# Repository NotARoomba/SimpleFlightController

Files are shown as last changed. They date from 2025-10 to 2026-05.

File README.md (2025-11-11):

<h1 align="center">
  <br>
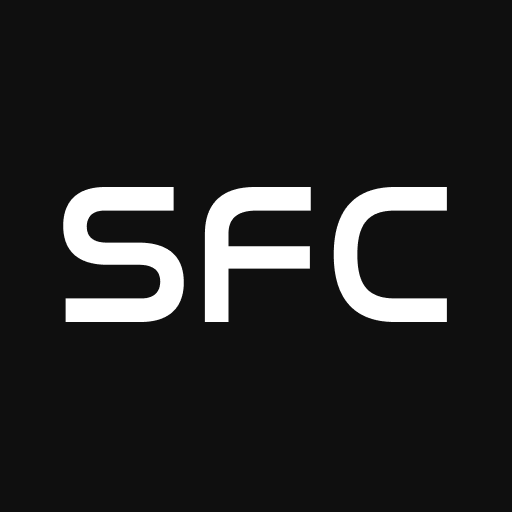
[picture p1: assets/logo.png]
SFC
  
  <br>
  Simple Flight Controller
  <br>
</h1>

<h4 align="center">
A comprehensive guide on building a flight controller from scratch for rockets!
</h4>

<div align="center">




</div>

<p align="center">
  <a href="#key-features">Key Features</a> •
  <a href="#guide">Guide</a> •
  <a href="#pcb">PCB</a> •
  <a href="#credits">Credits</a> •
  <a href="#license">License</a>
</p>

Flight Controller PCB

## Key Features

- **STM32F722RET6 microcontroller** for high-performance control
- **ICM-45686 IMU** for precise motion tracking
- **BMP580 barometer** for altitude sensing
- **MicroSD card storage** for flight data logging
- **Dual servo outputs** for TVC or fin control
- **2-cell LiPo support** with integrated BQ25883 charger
- **USB-C connectivity** for programming and data transfer
- **Compact design** optimized for rocket applications

## Guide

Check out the comprehensive [GUIDE.md](GUIDE.md) that walks you through:

- Component selection and requirements
- Schematic design with detailed explanations
- Communication protocols (I2C, SPI, UART, USB)
- PCB layout and routing best practices
- Power management circuitry
- Manufacturing with JLCPCB

## PCB

Designed in KiCad with careful attention to signal integrity, power distribution, and compact layout suitable for rocket applications.

### Schematic

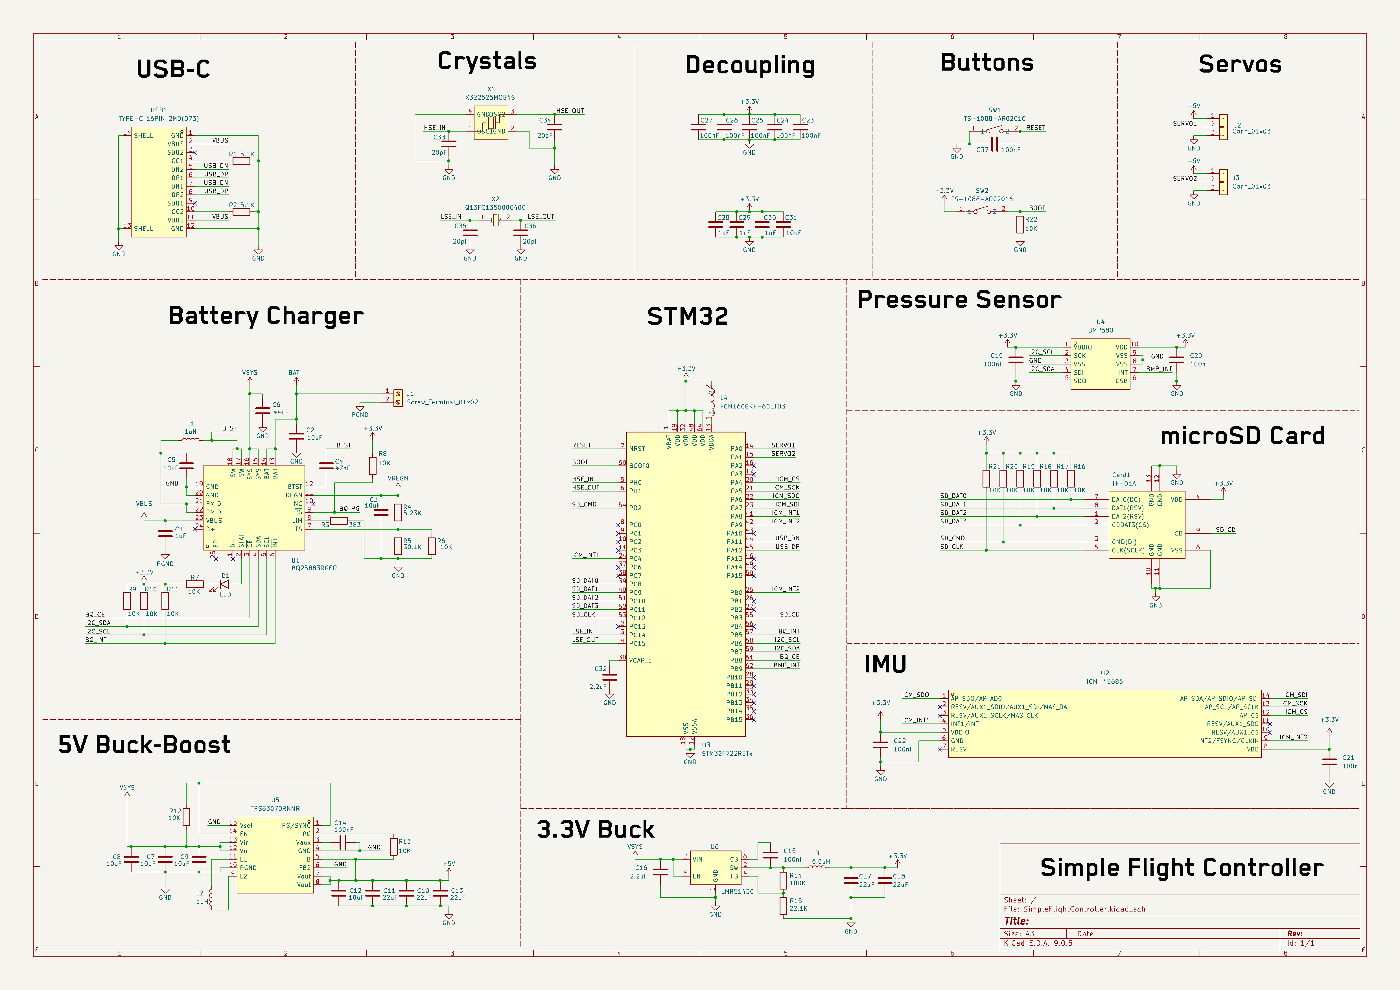
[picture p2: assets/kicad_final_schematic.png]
Schematic


### PCB Layout

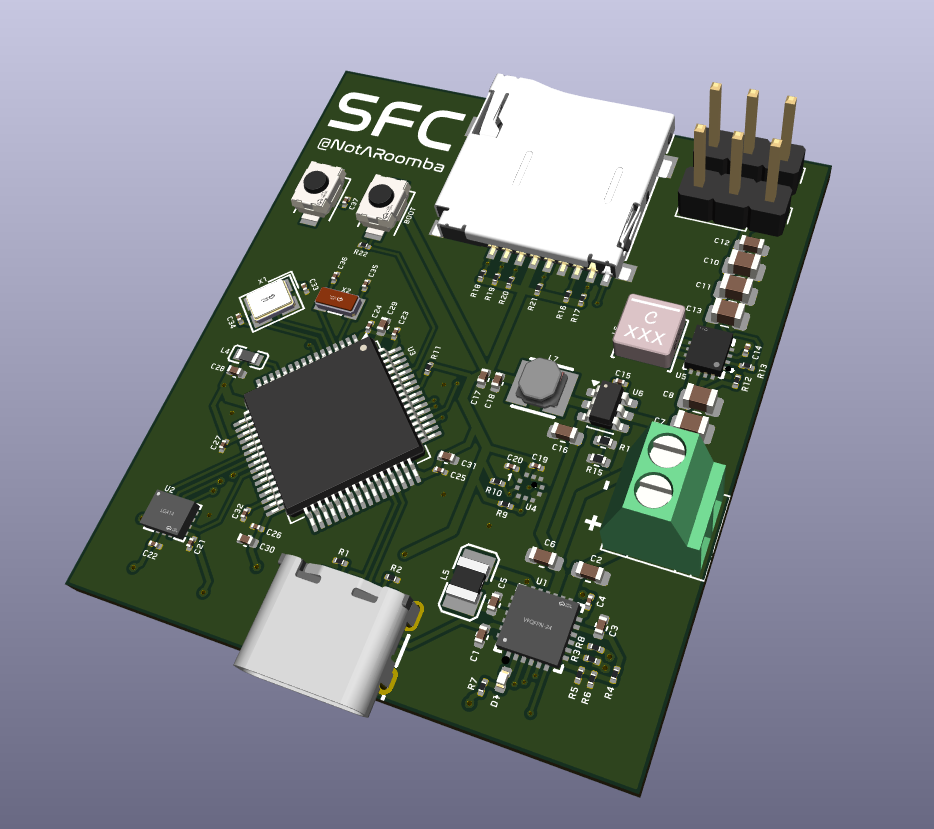
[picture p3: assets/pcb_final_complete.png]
PCB Layout


## Credits

This project uses:

- [KiCad](https://www.kicad.org/)
- [STM32CubeMX](https://www.st.com/en/development-tools/stm32cubemx.html)
- [easyeda2kicad.py](https://github.com/uPesy/easyeda2kicad.py)
- [Hack Club Blueprint](https://blueprint.hackclub.com/)

## You may also like...

- [Trace](https://github.com/NotARoomba/Trace) – A comprehensive PCB ruler with reference footprints
- [Cyberboard](https://github.com/NotARoomba/Cyberboard) – A Raspberry Pi Pico-sized STM32 development board with Bluetooth
- [CyberCard](https://github.com/NotARoomba/CyberCard) – A Cyberpunk themed NFC hacker card
- [Niveles De Niveles](https://github.com/NotARoomba/NivelesDeNiveles) – Real-time flood alert app
- [Linea](https://github.com/NotARoomba/Linea) – An EMR tablet
- [Tamaki](https://github.com/NotARoomba/Tamaki) – A cute HackPad

## License

MIT

---

> [notaroomba.dev](https://notaroomba.dev) &nbsp;&middot;&nbsp;
> GitHub [@NotARoomba](https://github.com/NotARoomba) &nbsp;&middot;&nbsp;

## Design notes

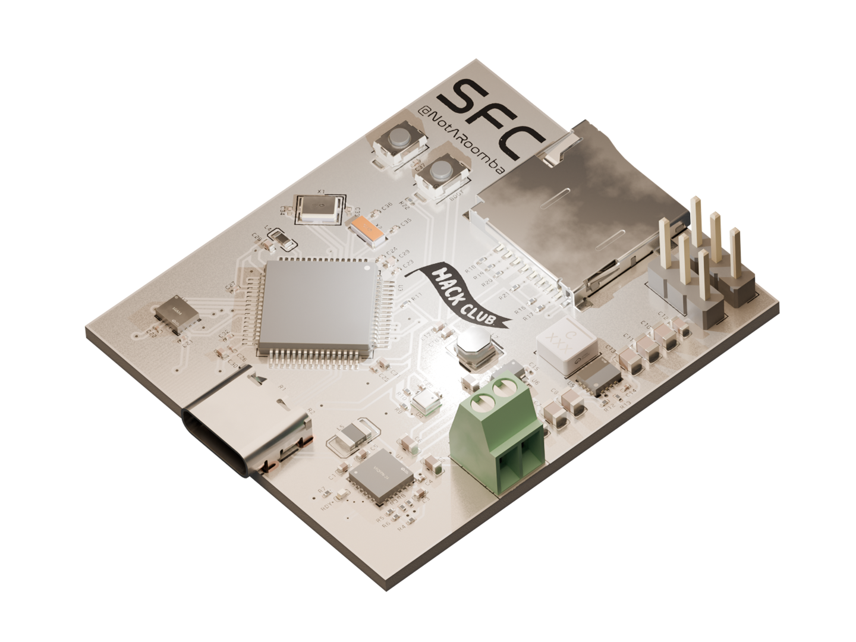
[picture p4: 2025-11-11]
blender/render_cropped.png

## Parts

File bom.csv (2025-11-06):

Item | Price | Source
PCB | 165.50 | JLCPCB

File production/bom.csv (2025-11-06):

Designator | Footprint | Quantity | Value | LCSC Part #
BOOT, RESET | SW-SMD_L3.9-W3.0-P4.45 | 2 | TS-1088-AR02016 | C720477
C1, C28, C29, C30 | 0402 | 4 | 1uF
C10, C11, C13 | 0805 | 3 | 22uF
C12, C2, C9 | 0603 | 3 | 10uF
C14, C15, C19, C20, C21, C22, C23, C24, C25, C26, C27, C37 | 0201 | 12 | 100nF
C16 | 0603 | 1 | 2.2uF
C17, C18 | 0402 | 2 | 22uF
C3, C31, C5 | 0402 | 3 | 10uF
C32 | 0201 | 1 | 2.2uF
C33, C34, C35, C36 | 0201 | 4 | 20pF
C4 | 0201 | 1 | 47nF
C6 | 0603 | 1 | 44uF
C7, C8 | 0805 | 2 | 10uF
CARD1 | TF-SMD_TF-01A | 1 | TF-01A | C91145
D1 | 0402 | 1 | LED
J1 | TerminalBlock_Xinya_XY308-2.54-2P_1x02_P2.54mm_Horizontal | 1 | Screw_Terminal_01x02
J2, J3 | PinHeader_1x03_P2.54mm_Vertical | 2 | Conn_01x03
L4 | L0603 | 1 | FCM1608KF-601T03 | C141723
L5 | L2520 | 1 | DFE252012F-1R0M=P2 | C435392
L6 | IND-SMD_L4.0-W4.0-A | 1 | XFL4020-152MEC | C3033018
L7 | IND-SMD_L3.0-W3.0 | 1 | YHNR3015-5R6M | C18236327
R1, R2 | 0201 | 2 | 5.1K
R10, R11, R12, R13, R16, R17, R18, R19, R20, R21, R22, R6, R7, R8, R9 | 0201 | 15 | 10K
R14 | 0402 | 1 | 100K
R15 | 0402 | 1 | 22.1K
R3 | 0201 | 1 | 383
R4 | 0201 | 1 | 5.23K
R5 | 0201 | 1 | 30.1K
U1 | VFQFPN-24_L4.0-W4.0-P0.50-BL-EP2.8 | 1 | BQ25883RGER | C544362
U2 | LGA-14_L3.0-W2.5-P0.50-TL | 1 | ICM-45686 | C22459454
U3 | LQFP-64_10x10mm_P0.5mm | 1 | STM32F722RETx
U4 | LGA-10_L2.0-W2.0-P0.50-TL_BMP580 | 1 | BMP580 | C22391138
U5 | VQFN-HR-15_L3.0-W2.5-P0.50-BL_TPS63070RNMR | 1 | TPS63070RNMR | C109322
U6 | SOT-23-6 | 1 | LMR51430
USB1 | USB-C-SMD_TYPE-C-6PIN-2MD-073 | 1 | TYPE-C 16PIN 2MD(073) | C2765186
X1 | CRYSTAL-SMD_4P-L3.2-W2.5-BL | 1 | X322525MOB4SI | C9006
X2 | FC-135R_L3.2-W1.5 | 1 | Q13FC1350000400 | C32346

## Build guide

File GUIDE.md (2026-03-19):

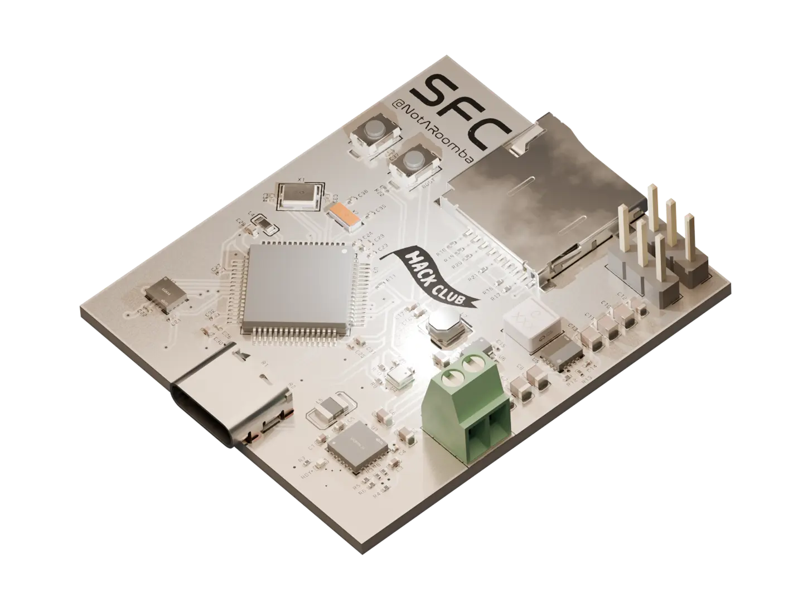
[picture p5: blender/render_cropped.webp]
Flight Controller Render


# How to make a flight controller (from scratch)

Made by @NotARoomba

This is an advanced project. I recommend learning the basics of KiCad by making a small dev board or breadboard first. That said, anyone can follow along, as I'll go **_in-depth_** on how to build a flight controller.

I'm [@NotARoomba](https://github.com/notaroomba) and I have a (sort of) obsession with making flight controllers so heres a guide so that you too have the knowledge of making something [cool](https://github.com/notaroomba/athena). The files for this guide can be found [here](https://github.com/notaroomba/simpleflightcontroller)

First, define what type of flight controller you want: for a rocket or a drone? Keep that in mind when starting your own design. In this guide, we'll build a flight controller specifically for rockets.

To start, create a new repository on GitHub and add two folders: `hardware` and `software`. These folders will hold most of the project files. Then, create a new KiCad project inside the `hardware` folder.

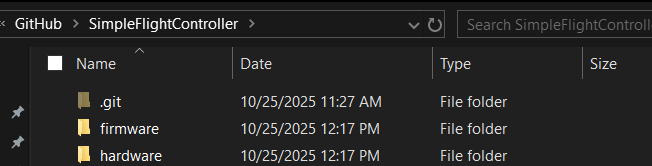
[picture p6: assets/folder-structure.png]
Folder Structure

(Folder structure)

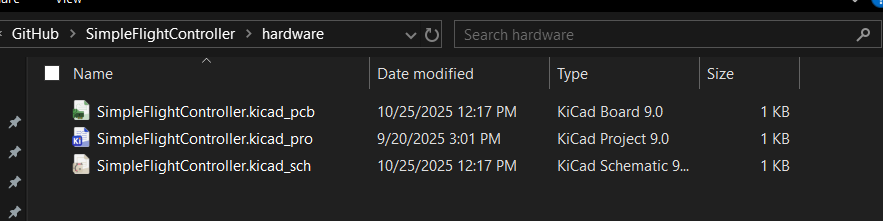
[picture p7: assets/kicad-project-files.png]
KiCad Project Files

(KiCad project files)

## Feature Definition

Before starting any engineering project, define the problem you're solving and the constraints you have. Imagine you want to build a rocket. All flight controllers include a `microcontroller`, which is a small computer that can be programmed to do various tasks. To control the rocket's flight, you'll use servos to move fins or a TVC system (`Thrust Vector Control`- tilting the engine nozzle to steer the rocket).

If you only build a board to drive servos, the rocket won't know which way it's pointing or how to correct its trajectory. You also need position and motion data (rotation and acceleration), plus altitude data. Finally, you'll want to store data persistently (even when powered off) for debugging and post-flight analysis.

Now that we have the rocket's functionality defined, we also need a way to power it. We can use a battery that can power both the rocket's computer and its servos.

Putting this together, we want these features in our rocket's flight controller:

- Can control servos for fins or TVC
- Can obtain position and altitude data
- Can store data even when powered off
- Can be powered by a battery

## Next steps

Now that we have our requirements, let's see how to meet them. Some requirements depend on others. For example, we want battery power - but how large should the battery be? That depends on the voltages and current the servos and microcontroller need, so let's define those first.

Depending on the size of your rocket, current needs will vary because larger servos draw more current. Most hobby servos run on 5–6V and draw ~1A. A 2-cell LiPo (Lithium Polymer) battery (7.4V nominal) is common in RC applications (each cell is ~3.7V) and can be regulated down to 5V for servos.

Most microcontrollers and sensors run on 3.3V, so with a 2-cell (7.4V) LiPo we have more than enough input voltage—as long as we regulate it down to a clean 3.3V line.

Now, after checking off one of the features, we need to tackle the three others.

- Can control servos for fins or TVC
- Can obtain position/altitude data
- Can store data even when powered off
- ~~Can be powered by a battery~~

After choosing servos, we need to know how to control them. Most hobby servos use `PWM (Pulse Width Modulation)`—a method of control where the microcontroller sends rapid on/off pulses, and the pulse width (duration) determines the servo's position.

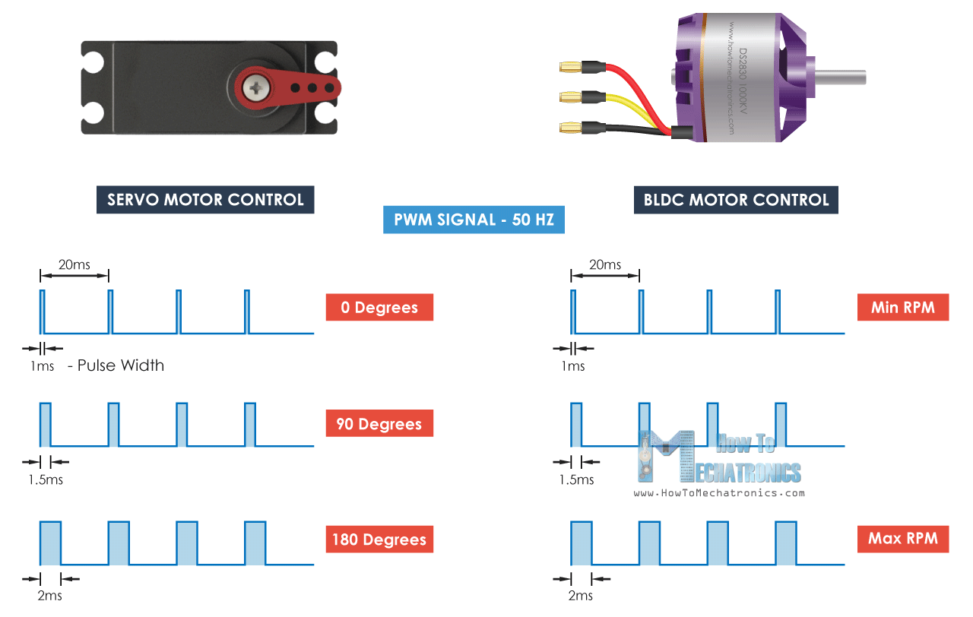
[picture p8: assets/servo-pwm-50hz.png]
Servo PWM Signal


The `duty cycle` is the percentage of the period that the signal is high (on).

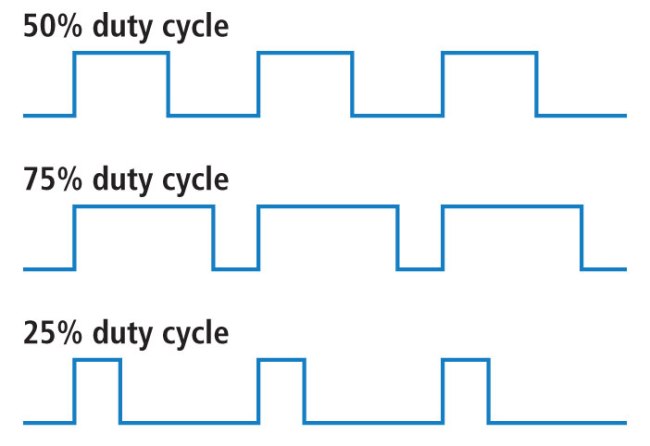
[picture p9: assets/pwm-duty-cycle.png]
PWM Duty Cycle


## What about the sensors and microcontroller?

- ~~Needs to be able to control servos for fins or TVC~~
- Needs a way to get position/altitude data
- Needs to store data even when the rocket is off
- ~~Needs to be able to be powered by a battery~~

For position and motion data, we use an `IMU`—an Inertial Measurement Unit. The IMU measures acceleration and rotation (and some devices also estimate altitude). We'll use the `ICM-45686`. While there are many IMUs with different features, this one is robust and well-supported.

For altitude, we'll use a dedicated sensor called a barometer. It measures air pressure and uses that to estimate altitude. We'll use the `BMP580`—a versatile and common choice for flight controllers.

Finally, to store data, we'll use a microSD card. While you can use onboard flash, microSD is more versatile when you want to access flight logs directly from a computer.

Now that we've defined the sensors and peripherals, we need to select a microcontroller. In this tutorial, we'll use an STM32, but you can adapt it to another MCU like the ESP32 if you want Bluetooth/Wi-Fi support. I prefer STM32 because it's relatively easy to program and widely used in flight controllers. After reviewing STM32 options, we'll use the STM32F722RET6 for its high clock speed and lots of peripherals. Feel free to choose another package or part for larger designs.

- ~~Needs to be able to control servos for fins or TVC~~
- ~~Needs a way to get position/altitude data~~
- ~~Needs to store data even when the rocket is off~~
- ~~Needs to be able to be powered by a battery~~

## Power Management

We have two power sources: USB-C from your computer (5V) and a battery (about 7–8.4V for a 2-cell LiPo). You cannot just wire them together. They need circuitry to choose which one feeds the board and to set the right voltages. The microcontroller typically runs at 3.3V, so we must lower the voltage (from the battery or USB-C) before it reaches the MCU.

To change the voltages, we need to use a regulator. There are two common kinds of regulators you'll hear about:

- `LDO`—Low Dropout regulator. It only turns higher voltage into a slightly lower one. Easy and quiet, but it wastes the excess as heat.
- `Switching regulator`—A more efficient regulator. It can:
  - `buck` (turn higher voltage down),
  - `boost` (push lower voltage up), or
  - `buck-boost` (keep the output steady even if the input goes above or below it).

What we'll do on this board:

- Make a 3.3V line (for the MCU and sensors) using a buck regulator.
- Make a 5V line (for servos or accessories) using a buck-boost regulator so it stays at 5V even as the battery voltage fluctuates.
- Get a battery charging IC (Integrated Circuit—a chip) that can charge a 2-cell battery from 5V.

Now that we've specified what functionality we need, we need to select the chips that provide it. I personally love to use ICs from Texas Instruments as they have good documentation and a huge selection of power management chips for everything related to USB.

Go to their website (https://www.ti.com/), select "Products", then "Battery Management ICs", and finally "Battery Charging ICs". Here you can find all sorts of battery charging chips to fit your requirements for future projects.

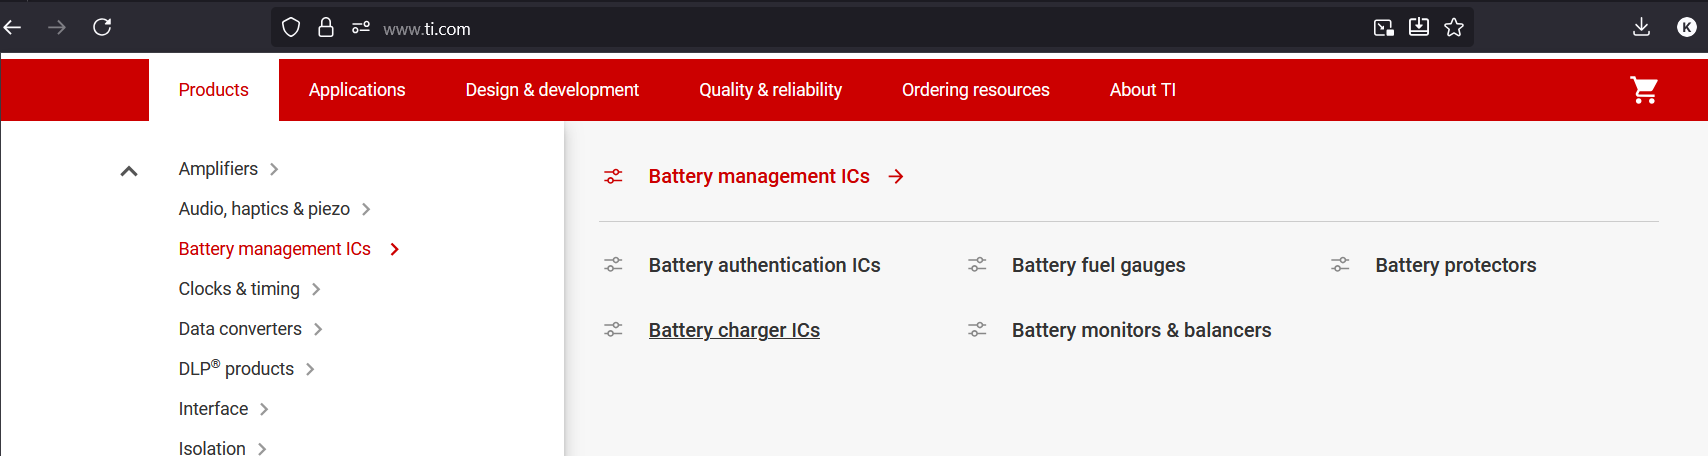
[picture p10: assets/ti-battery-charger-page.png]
TI Battery Charger Page


After looking around a bit, I found the `BQ25883`. It's a 2-cell Li-Ion/LiPo charger (which meets our requirement). You could add a more complicated battery charger if you want more cells/power, but they take up more space and are more complex to route.

For the regulators, go back to the TI main page, then navigate to "Power Management," then "DC/DC Power Modules." Here you can find all the regulators you would ever need, complete with excellent datasheets.

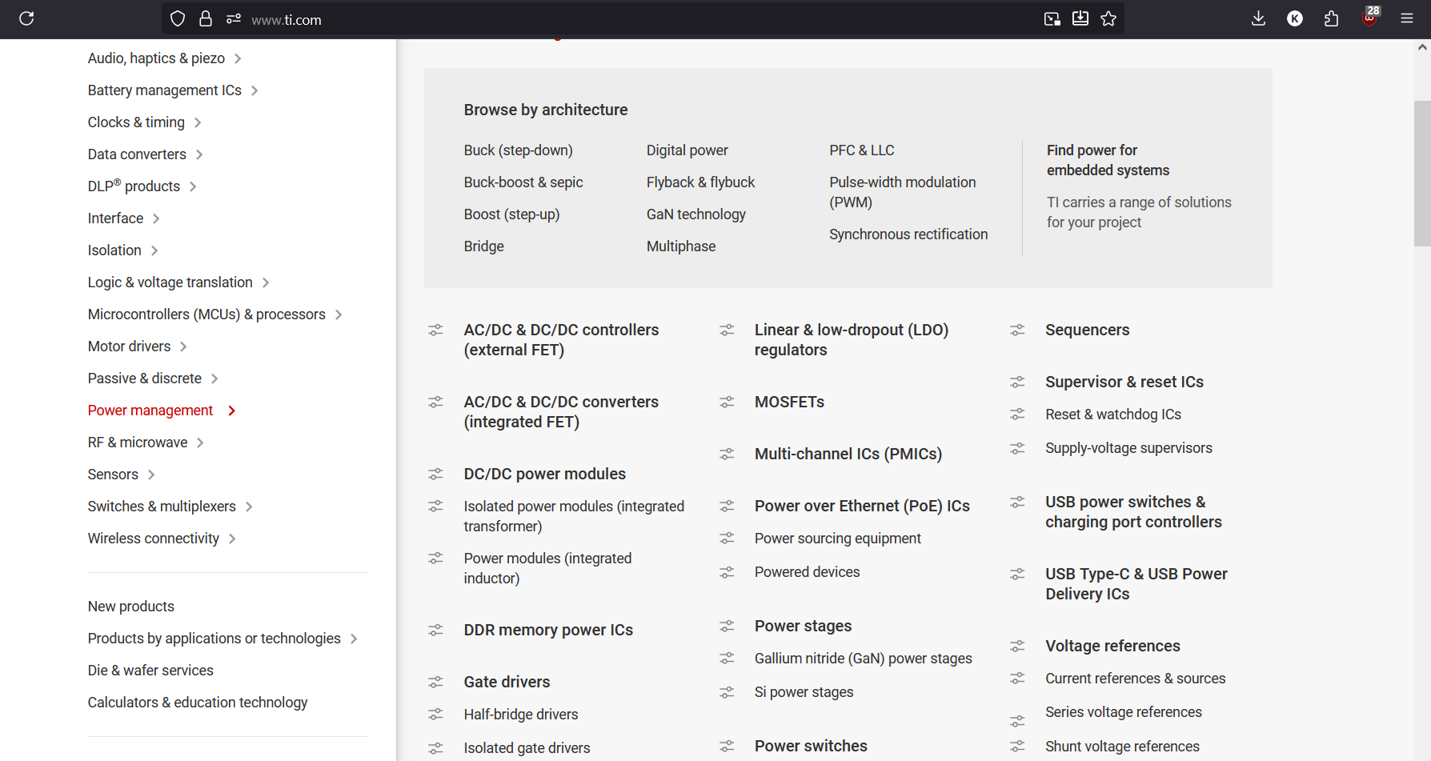
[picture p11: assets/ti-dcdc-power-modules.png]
TI DC/DC Power Modules


Here is where we can choose the right regulators for our needs. For this tutorial, we are going to use the `TPS63070`, which supports 2–16V input and can output a steady 5V with high current for the servos.

Now all that's missing is to find another regulator for 3.3V. For this, we are going to use the `LMR51430` as it supplies a lot of amperage for the various sensors that we will be using.

Now that we have the chips that we are going to use, we also need to verify that they are available on some platform like [LCSC](https://lcsc.com) or wherever else you are going to manufacture your PCB. We also might have to import certain components from LCSC into KiCad.

## Final component list

- USB-C
- MicroSD
- TPS63070
- LMR51430
- BQ25883
- STM32F722RETx
- ICM-45686
- BMP580
- Optional LED

# Starting the Schematic

Now that we have the components that we are going to use, let's start importing them into our project.

Although KiCad has a large selection of components, it is still a bit outdated and there are tons of chips that we would have to import in order to use them. Thankfully, there is a library called [`easyeda2kicad.py`](https://github.com/uPesy/easyeda2kicad.py) that can import these components from LCSC for us.

I have made a simple helper script to import all of the LCSC IDs from a text file, so all you have to do is append the part numbers and run the script again.

## Adding Custom Parts

Start by creating a folder called `lib` in the `/hardware` directory.

Then in the `/hardware` directory, create a new file called `lcsc.txt` and leave it empty for now.

Then create a file called `lcsc.py` (or whatever name you want) and paste this code in there:

```import argparse
import os
import shutil
import subprocess
import sys

def run_easyeda2kicad_from_file(input_file, output_dir="./lib/lcsc", python_exec="python"):
    input_file = os.path.expanduser(input_file)
    output_dir = os.path.expanduser(output_dir)
    python_exec = python_exec or "python"

    if not os.path.isfile(input_file):
        print(f"Error: File not found: {input_file}")
        return 2

    # If a simple name was provided, check PATH; if an absolute path, check that file exists.
    found = shutil.which(python_exec) if os.path.basename(python_exec) == python_exec else os.path.exists(python_exec)
    if not found:
        print(f"Warning: Python executable '{python_exec}' not found in PATH or as given path. Trying anyway.")

    os.makedirs(output_dir, exist_ok=True)

    with open(input_file, "r", encoding="utf-8") as f:
        # ignore blank lines and comments
        lines = [line.strip() for line in f if line.strip() and not line.lstrip().startswith("#")]

    if not lines:
        print("No LCSC IDs found in input file.")
        return 0

    for idx, lcsc_id in enumerate(lines, start=1):
        cmd = [
            python_exec,
            "-m", "easyeda2kicad",
            "--full",
            f"--lcsc_id={lcsc_id}",
            f"--output={output_dir}",
        ]
        print(f"[{idx}/{len(lines)}] Running: {' '.join(cmd)}")
        try:
            subprocess.run(cmd, check=True)
        except subprocess.CalledProcessError as e:
            print(f"❌ Error processing {lcsc_id}: {e}")
        except FileNotFoundError as e:
            print(f"❌ Executable not found: {e}")
            return 3

    print("✅ All commands completed.")
    return 0

def main(argv=None):
    parser = argparse.ArgumentParser(description="Run easyeda2kicad for a list of LCSC IDs.")
    parser.add_argument("input_file", nargs="?", default="./hardware/lcsc.txt", help="Path to file with one LCSC ID per line")
    parser.add_argument("output_dir", nargs="?", default="./lib/lcsc", help="Output directory")
    parser.add_argument("--python", dest="python_exec", default="python",
                        help="Python executable to use (default: 'python')")
    args = parser.parse_args(argv)

    return_code = run_easyeda2kicad_from_file(args.input_file, args.output_dir, args.python_exec)
    sys.exit(return_code if isinstance(return_code, int) else 0)

if __name__ == "__main__":
    main()
```

---

This code basically calls the `easyeda2kicad.py` library for every line that is present in `lcsc.txt` and adds it to a KiCad library in `/hardware/lib/lcsc`. (Make sure to install it first using `pip install easyeda2kicad.py`)

Now after creating both of those files, in your favorite IDE, edit `lcsc.txt` with the part numbers of the chips that you are going to use.

For example, let's say I want to add a USB-C port from LCSC. Go to [`www.lcsc.com`](www.lcsc.com) and search for USB-C.

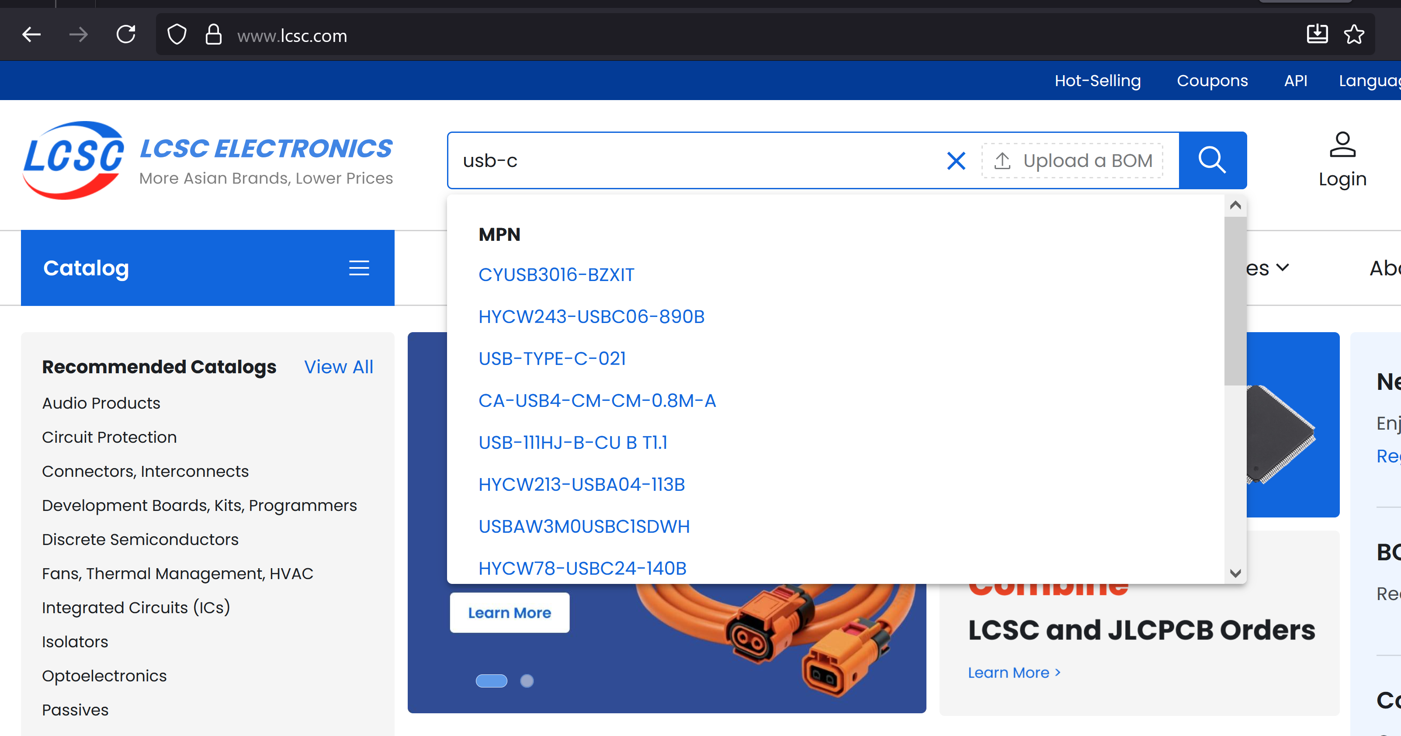
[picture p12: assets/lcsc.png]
LCSC Search


After searching, I found a good part with large stock (important!), so I then copy the part number (always starts with C followed by numbers, and it's under the name) into `lcsc.txt`.

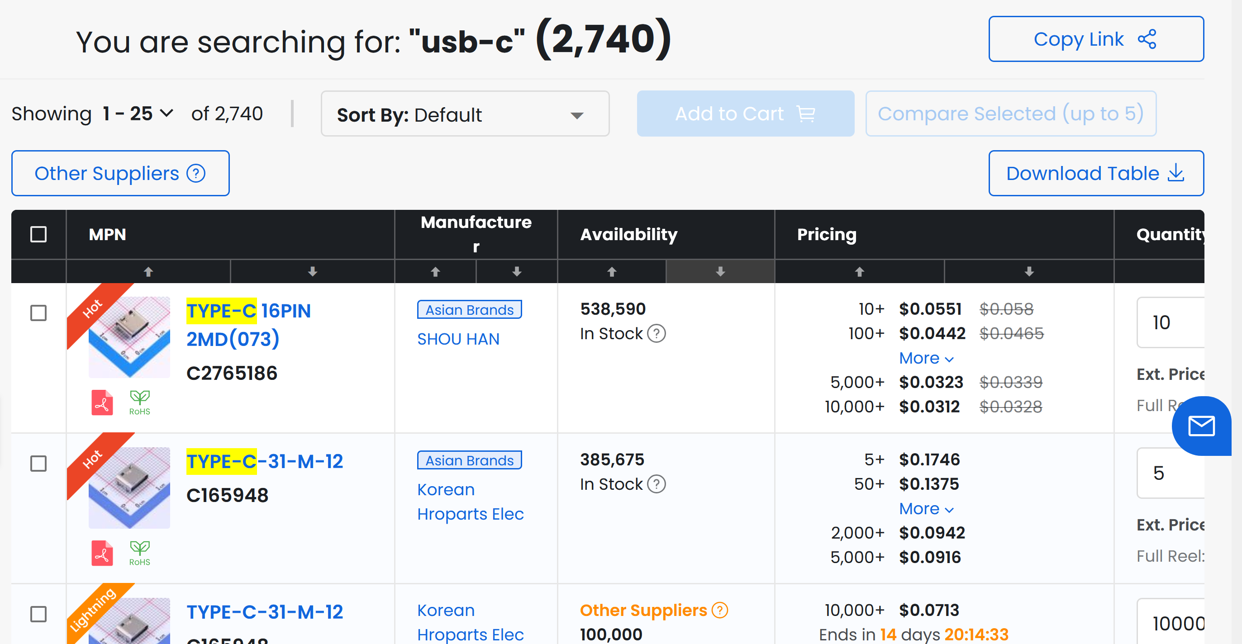
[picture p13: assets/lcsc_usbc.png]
LCSC Search


It should look like this:

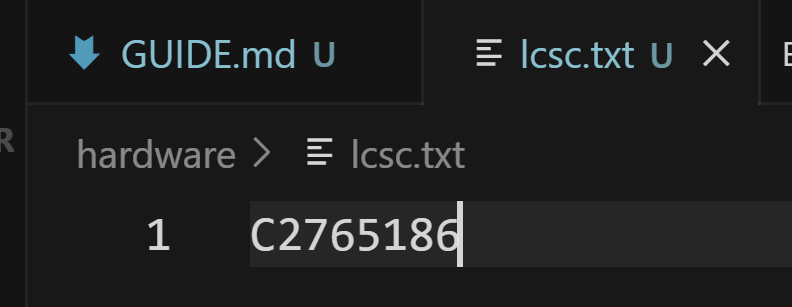
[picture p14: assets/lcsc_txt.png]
LCSC Search


Then run the Python script to convert that part number into a KiCad library. **IMPORTANT: YOU NEED TO RUN THE SCRIPT EVERY TIME YOU UPDATE `lcsc.txt`.** If you get an error that you can't find `lcsc.txt`, make sure to run the file from the root of your project or add arguments to specify the path of the library/lcsc txt file.

If you have done everything correctly, you should have something that looks like this:

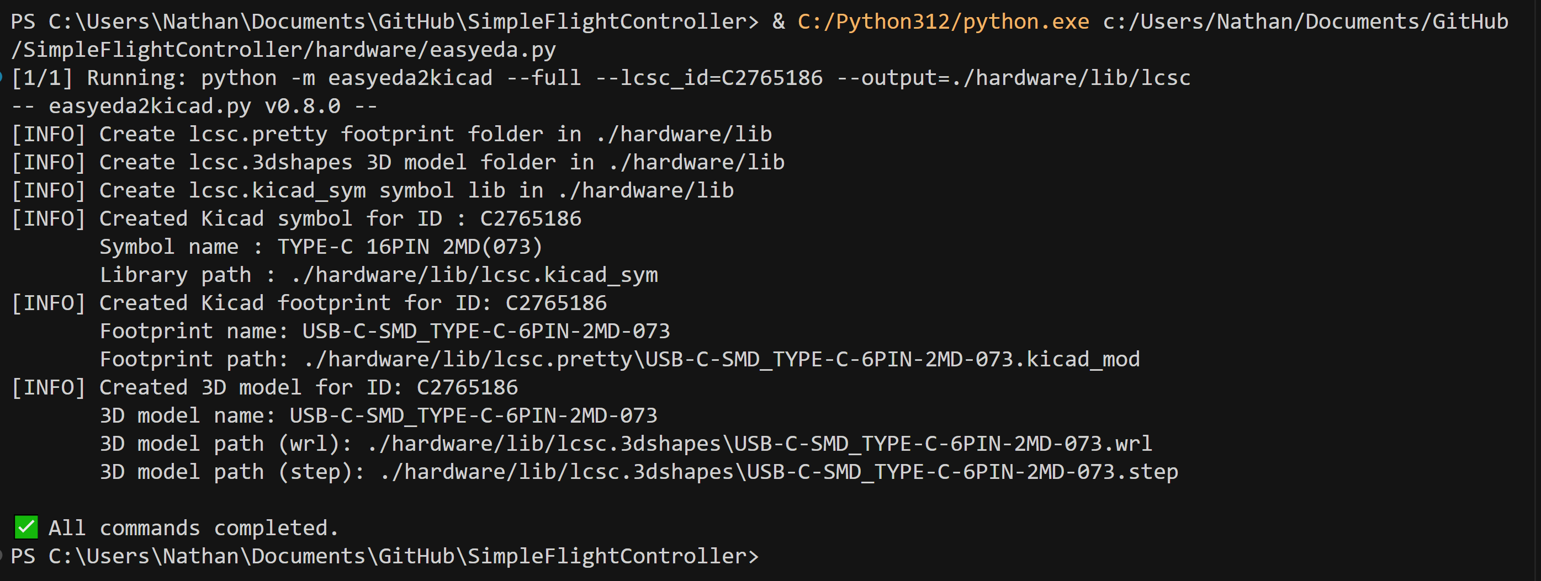
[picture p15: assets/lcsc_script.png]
LCSC Search


If in the future you get an error that the script couldn't find/parse a 3D model, those errors are safe to ignore as you can add the 3D model later. However, if the script can't find/parse a footprint for a specific part, then you should probably find another one on LCSC.

After running the script for the first time, add the library to your KiCad project and also the footprint library (the folder that ends with .pretty). It should look like this when you are done.

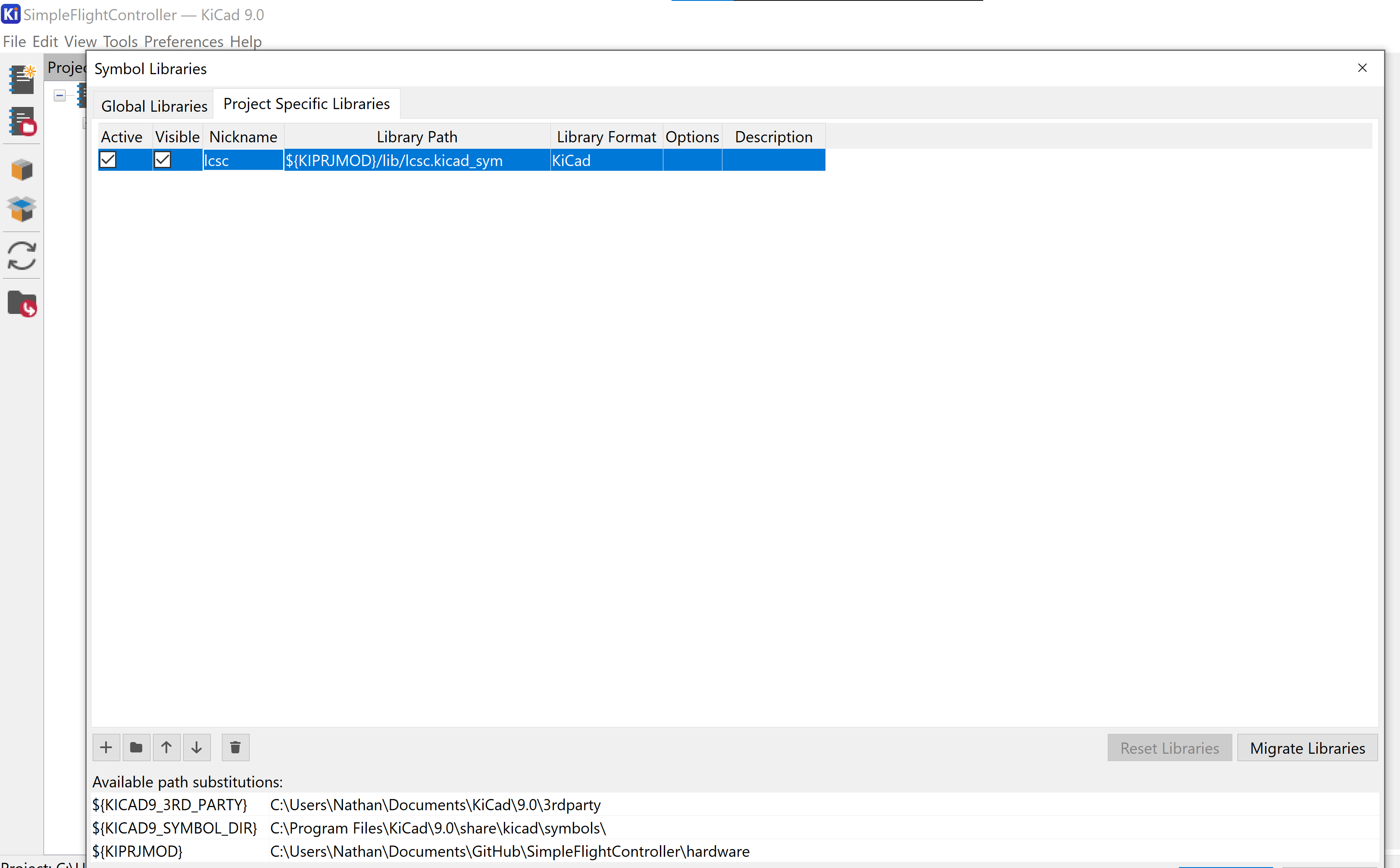
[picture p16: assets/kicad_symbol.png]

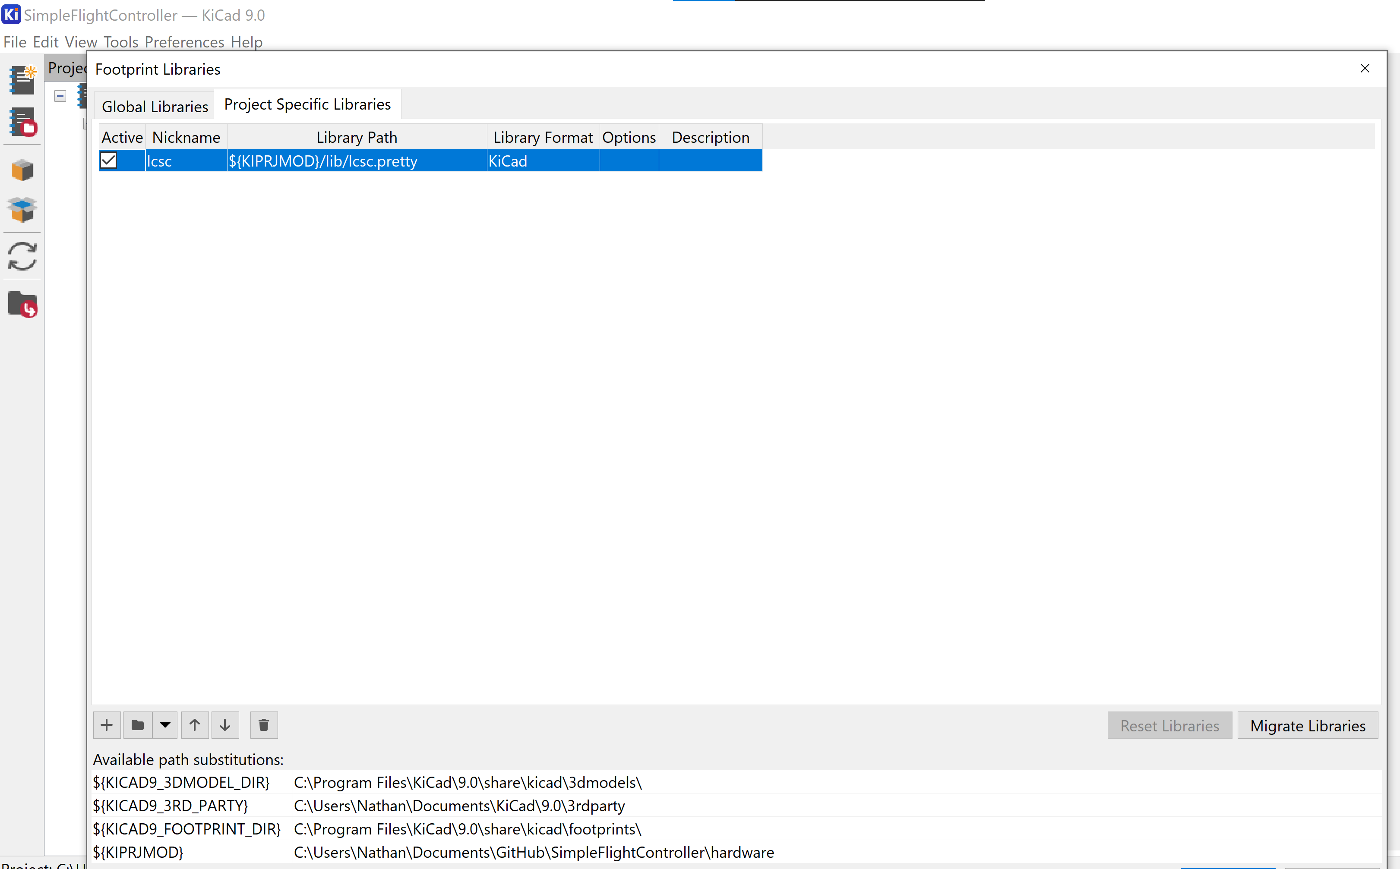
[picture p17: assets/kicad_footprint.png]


Then after that's done, go into your schematic and search for "lcsc". You should find the library with the USB-C connector (or whatever other part you imported).

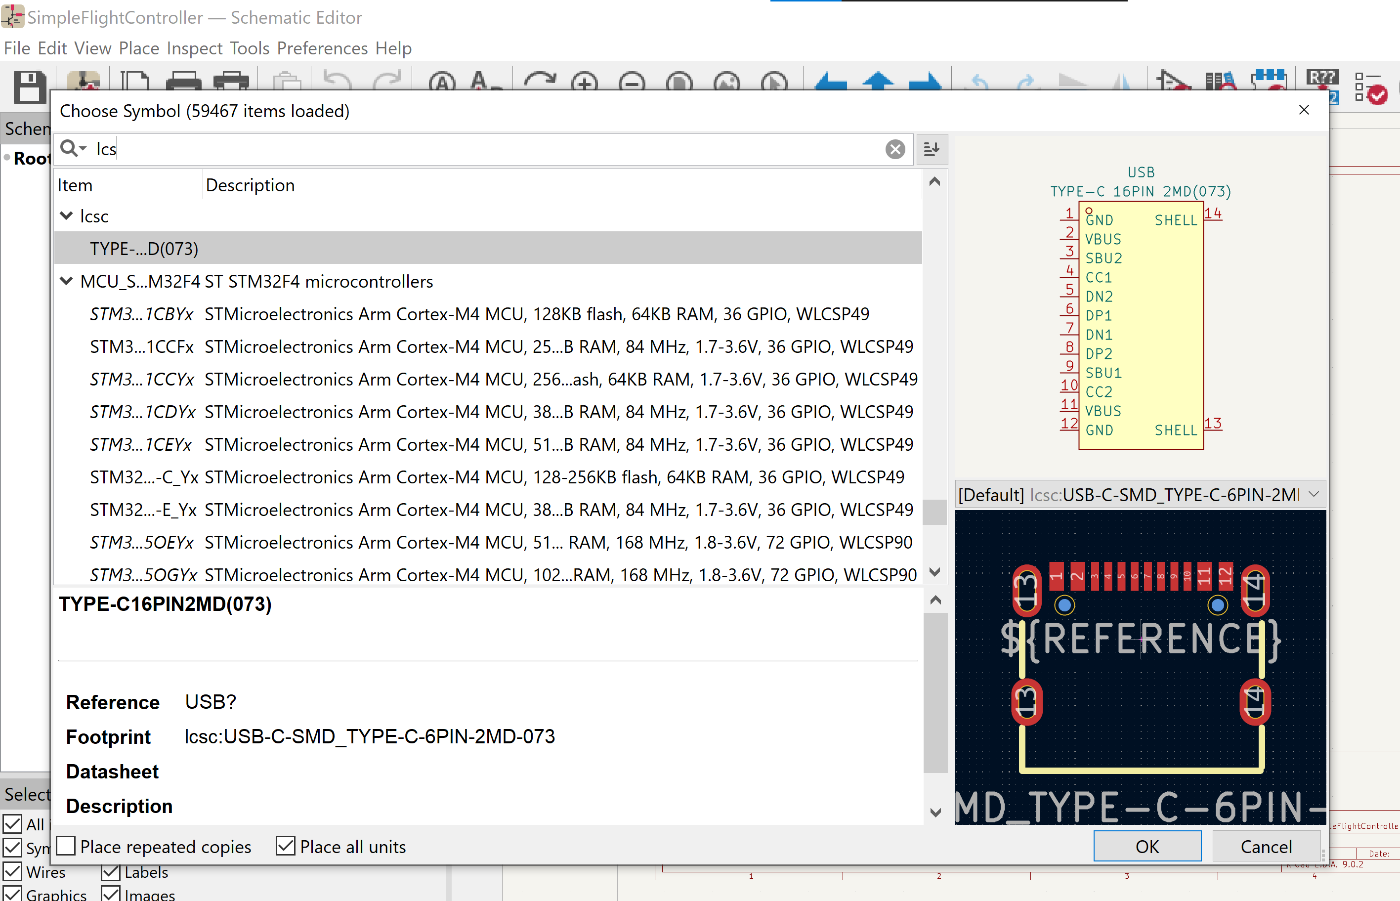
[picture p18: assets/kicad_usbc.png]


Keep in mind that there are some parts that KiCad already has, such as `STM32F722RETx`, but there are others like the IMU that you will have to import.

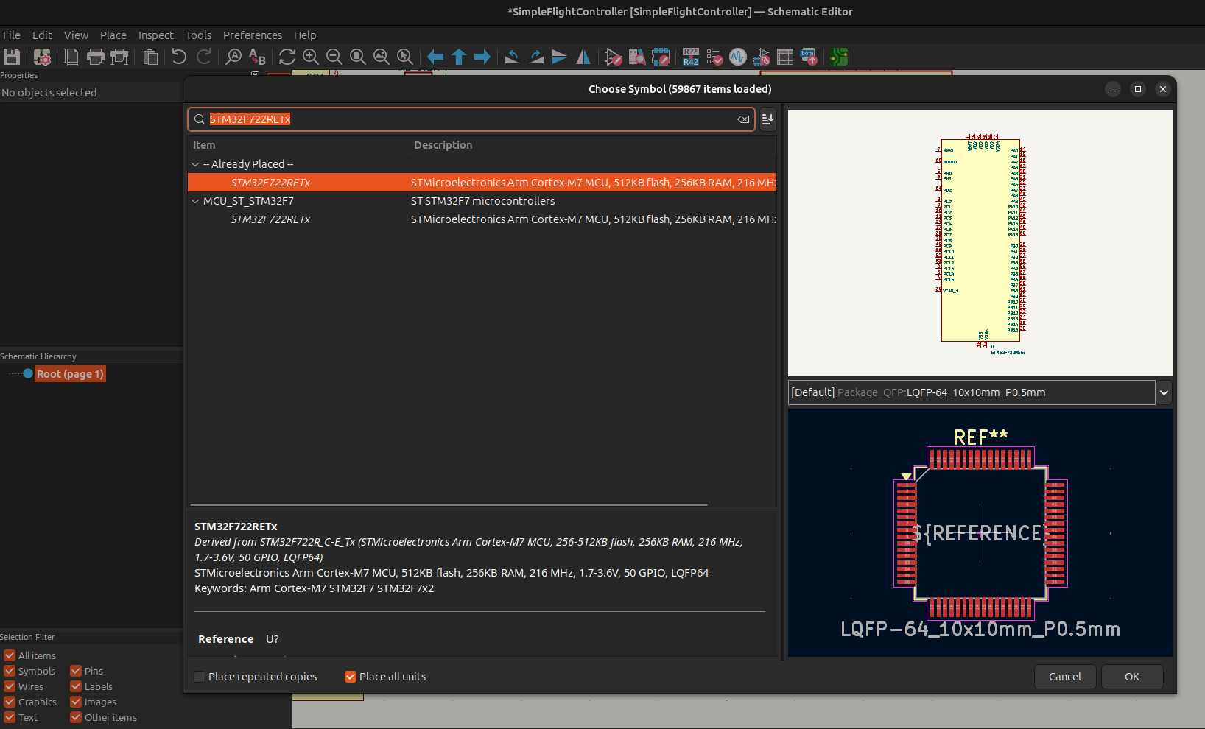
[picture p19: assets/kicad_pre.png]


After finding the components on LCSC, my `lcsc.txt` looks like this:

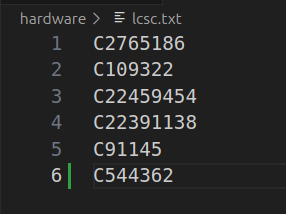
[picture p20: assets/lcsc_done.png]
LCSC Search


Now run the script again. Once it's done, go back to KiCad and add in all of the components (you may have to reopen the choose parts screen for the LCSC library to update).

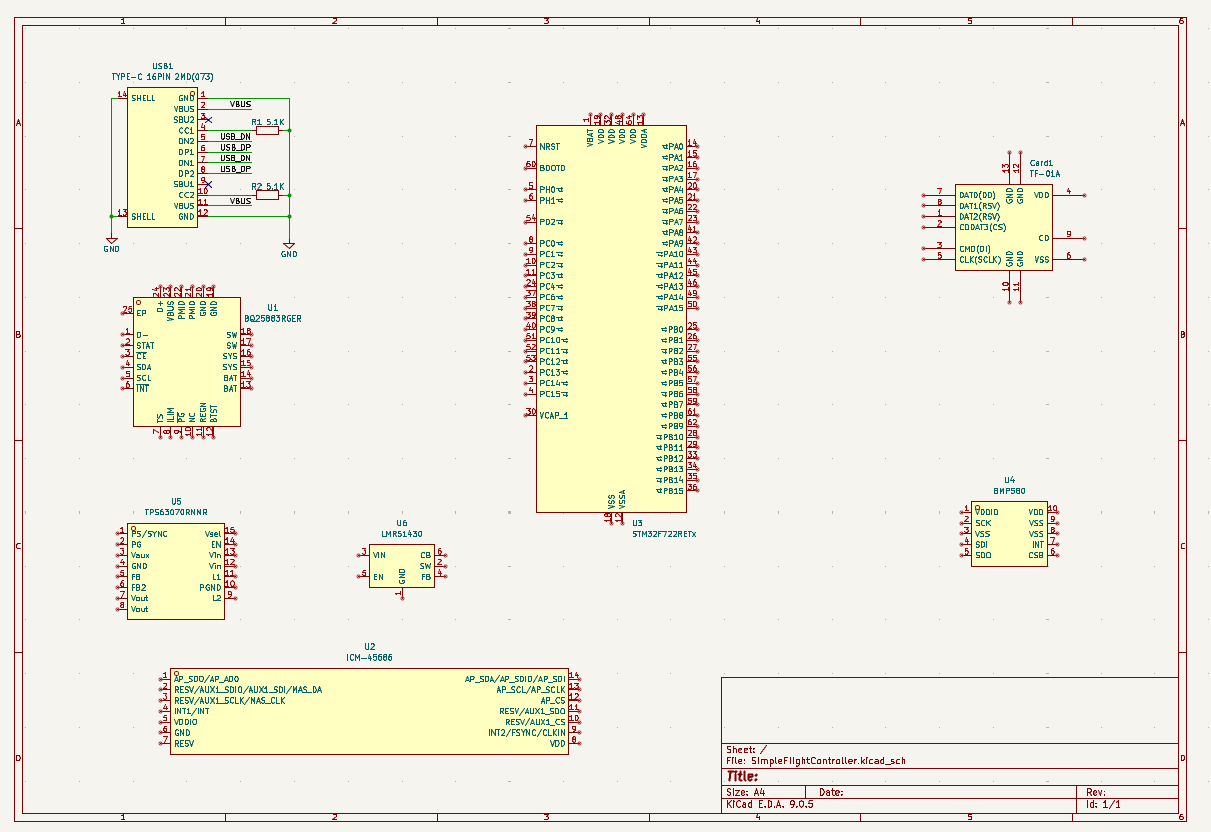
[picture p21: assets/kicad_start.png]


## USB-C and Power

Now let's start wiring up the power components and USB-C. It's always good practice to start wiring the components that would be used first. In this case, it would be USB-C as it is going to receive voltage, then the battery connector as that voltage from USB-C is going to directly charge the battery. If there is no USB-C, then the battery will provide voltage, followed by the 2 regulators. Again, you can wire each component up in whatever order. I just do it like this to be a bit more organized.

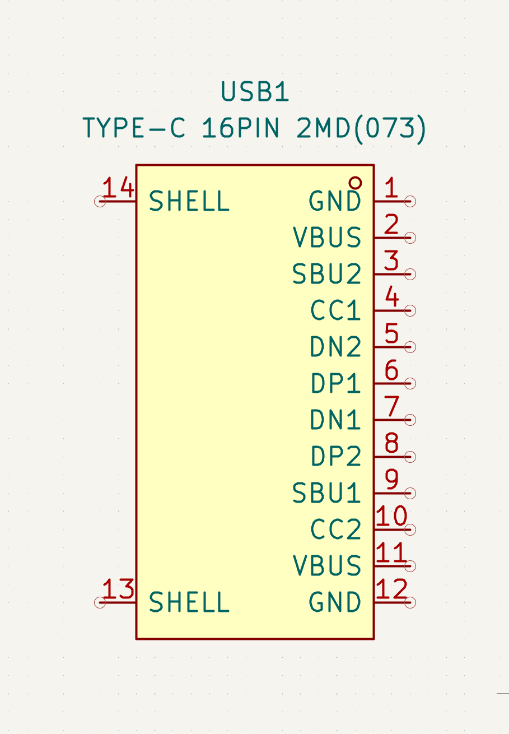
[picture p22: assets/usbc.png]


This is the USB-C connector. As you can see, it has a lot of pins, but don't worry if you don't know what all of those mean. Here's a quick explanation:

- **Shell**: This is the outer case of the USB-C port. It's usually connected to ground.
- **GND**: Ground.
- **VBUS**: This is the pin that supplies voltage from the device that connects to it. Usually it provides 5V at 3A, depending on the cable.
- **SBU1/2**: These are low-speed lines that can be used as alternate pins for different accessories, such as AUX+ and AUX- when connected to a DisplayPort. We don't need to use them.
- **CC1/2**: These are Configuration Channel pins. Basically, they detect if the connector is flipped and can also be used to negotiate more power out of VBUS (USB-PD). We are going to connect them to 5.1K resistors to ground as this tells the other device that we want 5V.
- **DN/DP**: These are the USB lines that we will be connecting to the STM32. They are used to transfer data between devices.

Now with that information in mind, when you finish wiring up the USB-C connector, it should look like this:

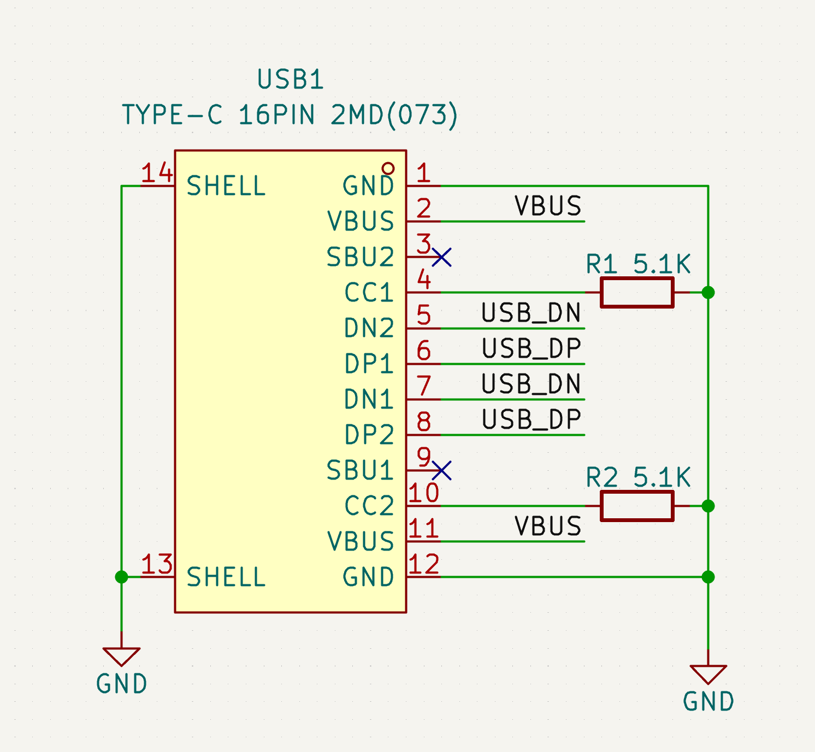
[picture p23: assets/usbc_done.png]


I used net labels to organize it better so that we don't have spaghetti cables all over the schematic.

### Battery Charger (BQ25883)

Now let's wire up the battery charger. This is the next step in our power route. There are many chips in the world, and knowing the pins on each of them is virtually impossible. So, each manufacturer provides what's called a `datasheet` for each component. It's basically a document that details everything about that chip—its pinout and how to implement it.

To access the datasheet for any component in KiCad, simply click on the component and press D. If there isn't one, just search on Google "`[part] datasheet`" and it's usually a PDF.

Opening the datasheet for the battery charger, we are greeted with this:

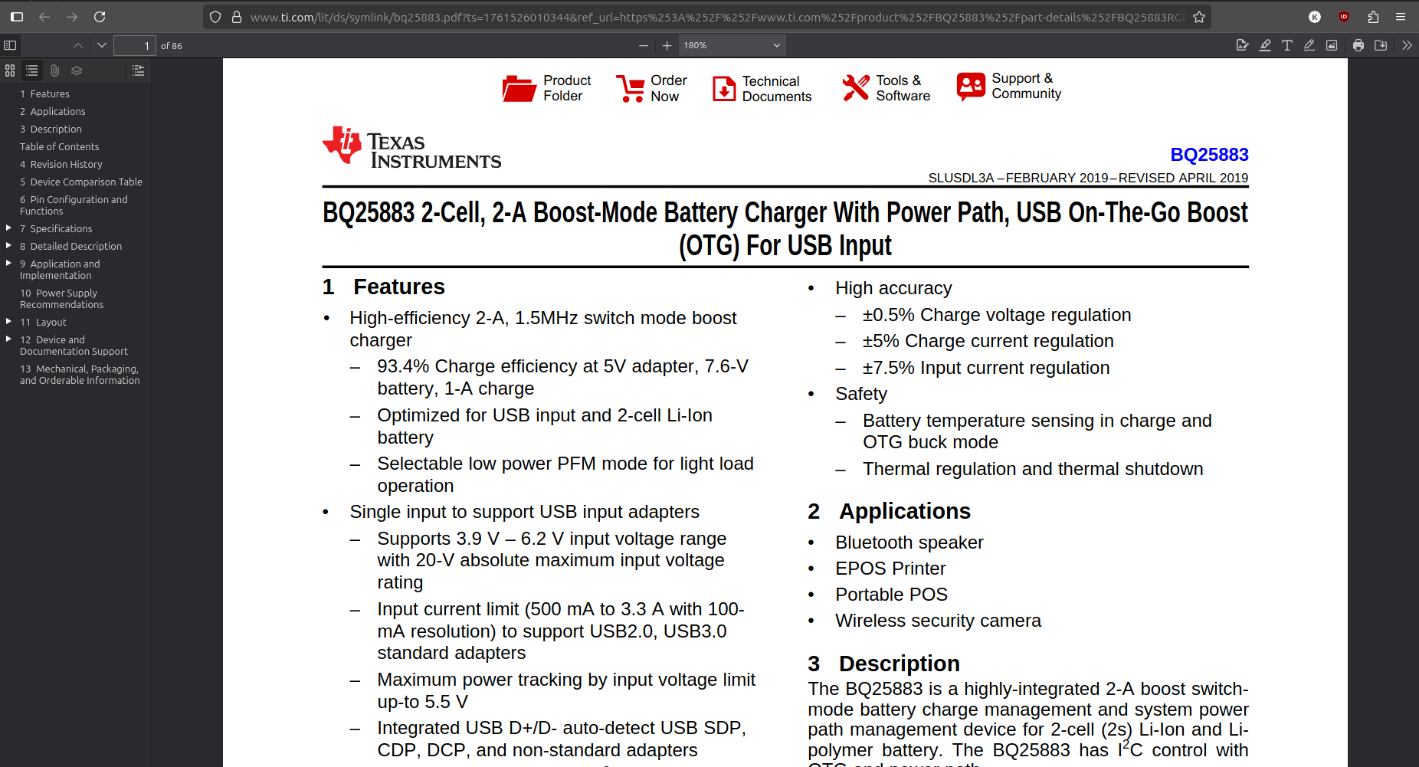
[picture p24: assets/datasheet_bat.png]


This may look intimidating as there are 86 pages of letters, numbers, formulas, and graphs. However, there is one section that is valuable to us called `Application and Implementation`. This section basically gives us a reference schematic on how to use said chip. We can use the sidebar or table of contents to locate that section. You should see this:

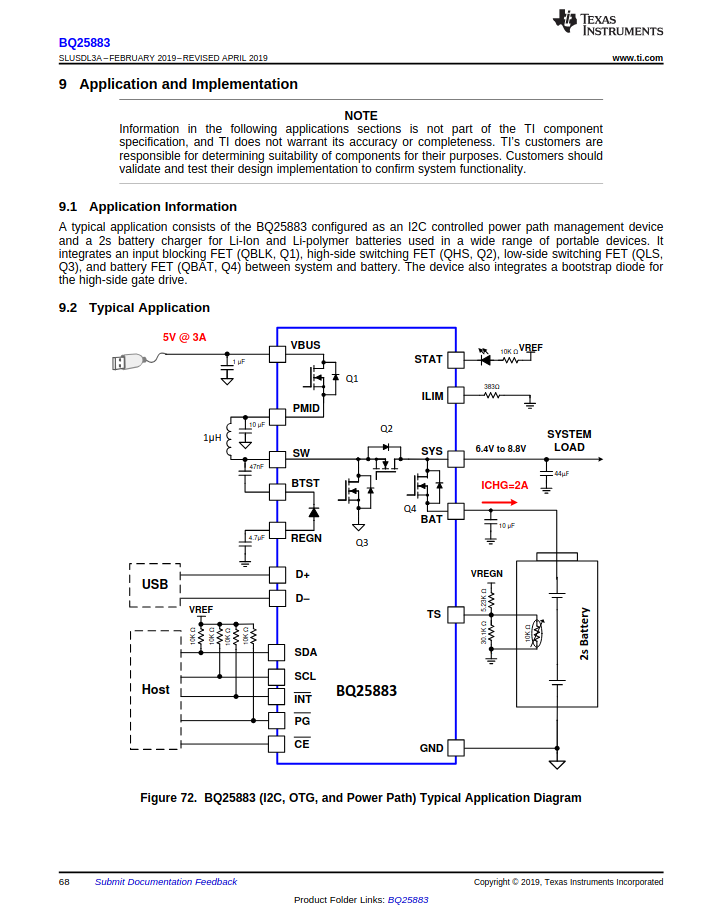
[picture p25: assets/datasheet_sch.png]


This is the schematic for a specific implementation, and we can see below that there is a table that describes it:

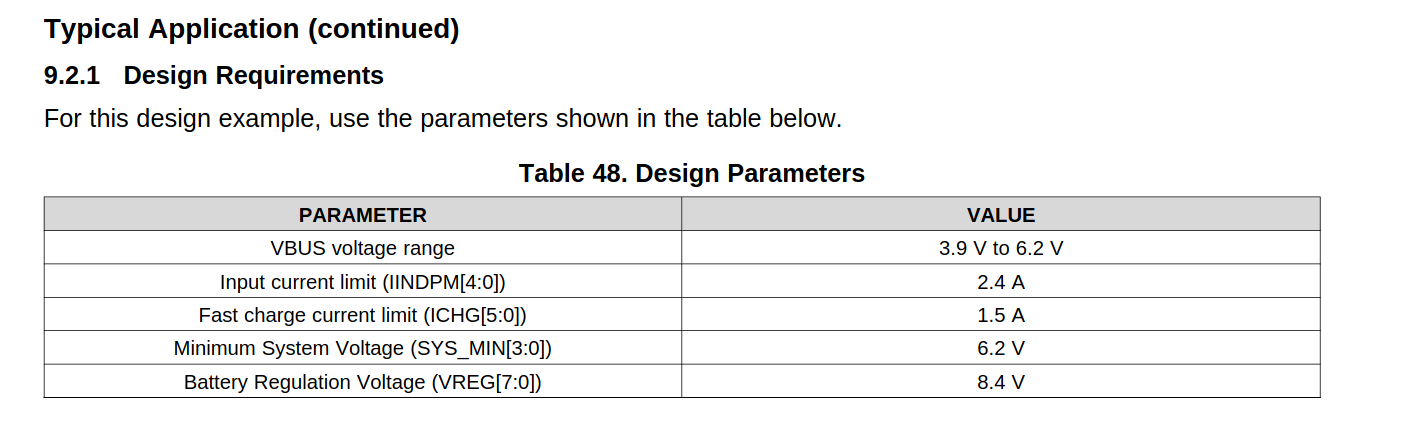
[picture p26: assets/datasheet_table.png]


Here we can see the different parameters that influence the design of the schematic above. It is important to understand what each of these values means to determine if the schematic works for your specific needs.

### Design Parameters Explained:

- **VBUS voltage**: How much voltage the chip needs to charge the battery. Our 5V from the USB-C fits within the range, so we're good.
- **Input current limit**: Determines how much of the available 3A current will be consumed.
- **Fast charge current limit**: Sets how much current will be used to charge the battery.
- **Minimum system voltage**: If the battery falls below this voltage, the internal regulator activates to maintain this voltage until the battery completely dies.
- **Battery regulation voltage**: The maximum voltage the chip will charge the batteries to. In this case: 4.2V per Li-ion cell × 2 cells = 8.4V maximum.

These parameters determine the specific resistor and capacitor values needed in the schematic. If we scroll down further in the datasheet, we can see the calculations needed to determine the inductor and capacitor values:

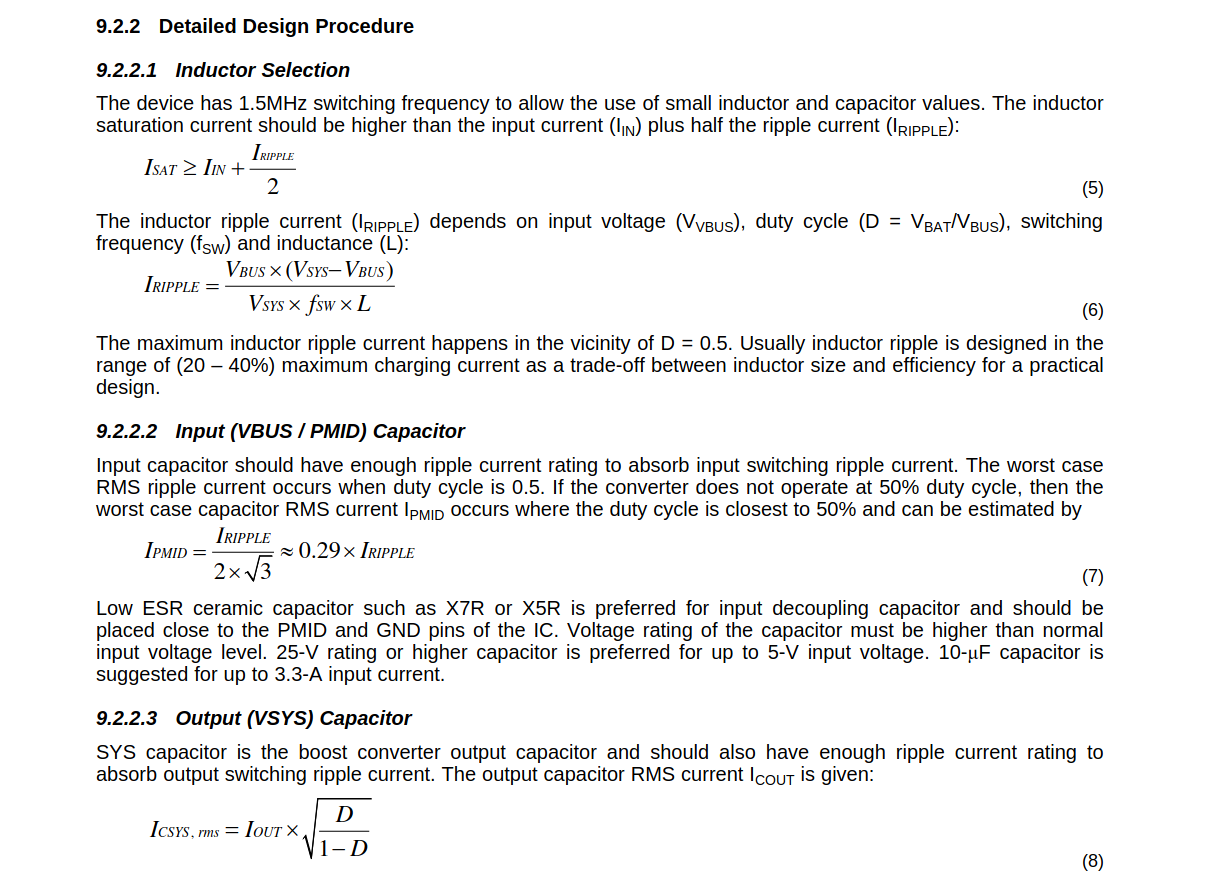
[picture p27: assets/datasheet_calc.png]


If you need a chip that has a reference schematic that doesn't fit your needs, then you need to do some calculations in order to get the right component values. However, usually you don't have to do that.

### Extra Info

If you haven't noticed already, the chip can be connected to a host through some pins called SDA, SCL, INT, CE, and PG. If you don't know what they do or want to know what they mean, there's a section in the datasheet called `Pin Configuration and Functions` that goes into detail about what each pin does.

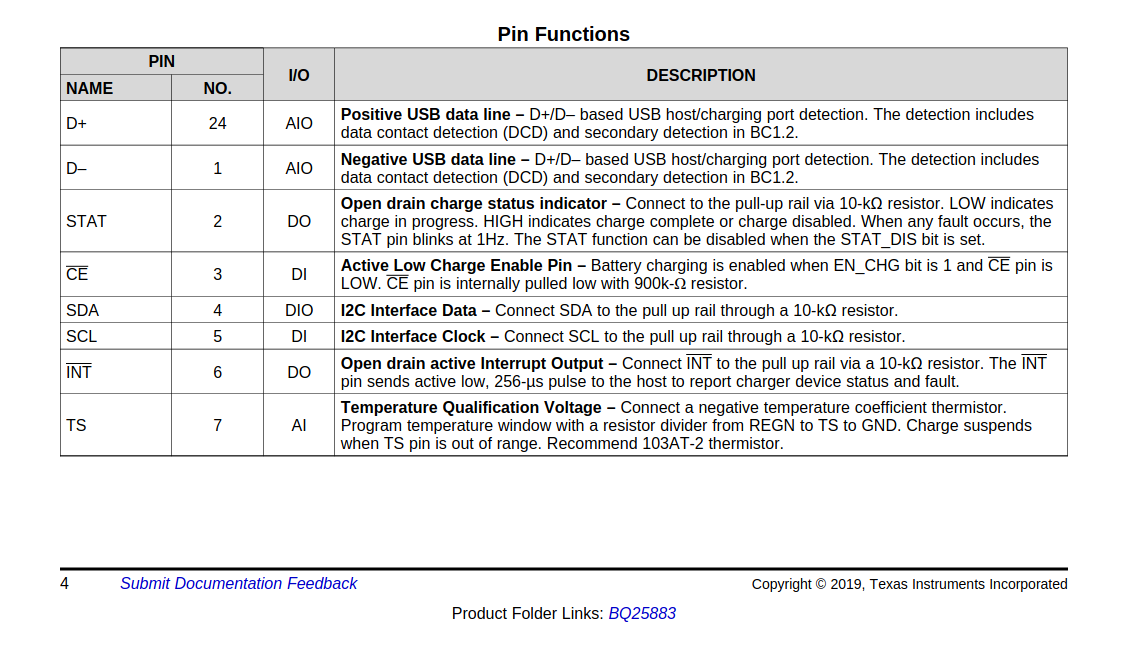
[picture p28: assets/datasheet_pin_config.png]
Datasheet Pin Configuration


Here we can see that for those pins there are descriptions like `active low`, `open drain`, and `I2C`. Let's break down what these terms mean:

#### Active Low

**Active low** means the pin is "active" (doing its job) when the voltage is LOW (0V or close to ground), not when it's HIGH (3.3V or 5V). Think of it like a backwards switch—when you pull the pin to ground, that's when it triggers the function. Many reset pins work this way: pull the reset pin low to reset the chip, and let it go high to run normally.

#### Open Drain

**Open drain** is a type of output that can only pull a pin down to 0V (LOW), but cannot push it up to 3.3V (HIGH). Think of it like a one-way switch—it can only connect the wire to ground, not to power. When the switch is "off", the wire is left floating with no connection. This is why open drain pins need a "pull-up resistor"—a resistor that connects the wire to 3.3V and keeps it HIGH when nothing is pulling it down. Multiple chips can share the same wire this way without interfering with each other.

### Communication Protocols

Now let's talk about the different ways chips can talk to each other. There are several common protocols you'll encounter:

#### I2C/I3C (Inter-Integrated Circuit)

I2C uses only **2 wires**: SDA (data) and SCL (clock). Multiple devices can share the same two wires, and each device has a unique address. Think of it like a conference call where everyone shares the same phone line, but each person has a unique ID. Both wires need one pull-up resistor each (in total) in order to function correctly.

**Pros:**

- Only needs 2 wires regardless of how many devices you connect.
- Built-in addressing system allows multiple devices on same bus.
- Relatively simple to implement.
- Good for sensors and simple peripherals.

**Cons:**

- Slower than SPI (typically 100 kHz to 3.4 MHz).
- Limited distance—long wires can cause signal problems.
- Can get complex with timing issues and error handling.
- Address conflicts if two devices have the same address.

#### SPI (Serial Peripheral Interface)

SPI uses **at least 3 wires** plus one additional wire for each device: MISO (Master In, Slave Out), MOSI (Master Out, Slave In), SCK (clock), and CS (Chip Select) for each device. It's like having separate phone lines for each conversation.

**Pros:**

- Much faster than I2C (can go 10 MHz+ easily).
- Full duplex (can send and receive simultaneously).
- Simpler protocol.
- More reliable over longer distances.

**Cons:**

- Needs more wires (especially with multiple devices).
- No built-in error checking.
- Only one master device allowed.
- Can use up many pins quickly with multiple devices.

#### UART (Universal Asynchronous Receiver-Transmitter)

UART uses **2 wires**: TX (transmit) and RX (receive). It's a point-to-point connection between two devices, like a private phone call.

**Pros:**

- Very simple—just 2 wires.
- No clock signal needed (asynchronous).
- Long distance capable with proper drivers.
- Universal—almost every microcontroller has it.
- Good for debugging and console output.

**Cons:**

- Only connects two devices directly.
- Both devices must agree on baud rate (how fast the data goes) beforehand.
- No built-in error correction.
- Can lose sync if timing is off.

#### USB (Universal Serial Bus)

USB uses **2 data wires** (D+ and D-) plus power and ground. It's like a smart postal system that can handle packages of different sizes and priorities.

**Pros:**

- Standardized connector and protocol.
- Provides power to devices.
- Hot-pluggable (can connect/disconnect while powered).
- High speed (up to 10 Gbps on USB 3.1).
- Built-in error correction and flow control.
- Can connect many devices through hubs.

**Cons:**

- Complex protocol requiring dedicated hardware/software.
- More expensive to implement.
- Requires specific connectors and cables.
- Power management can be tricky.
- Not suitable for real-time applications due to variable latency.

---

We will not be connecting the USB to the battery charging chip as we need to connect the STM32 to USB-C to be able to program it. Looking through the datasheet, it says that those pins are used to determine how much current can be used. However, they can also be set through the `I2C` interface that the IC has, so we can change that later with the STM32.

Now that we know that the schematic suits our needs, we can start copying it in KiCad. When copying a schematic from a datasheet, any pins that can be connected externally should use `Net Labels` like so (obviously with the pull-up resistors added later):

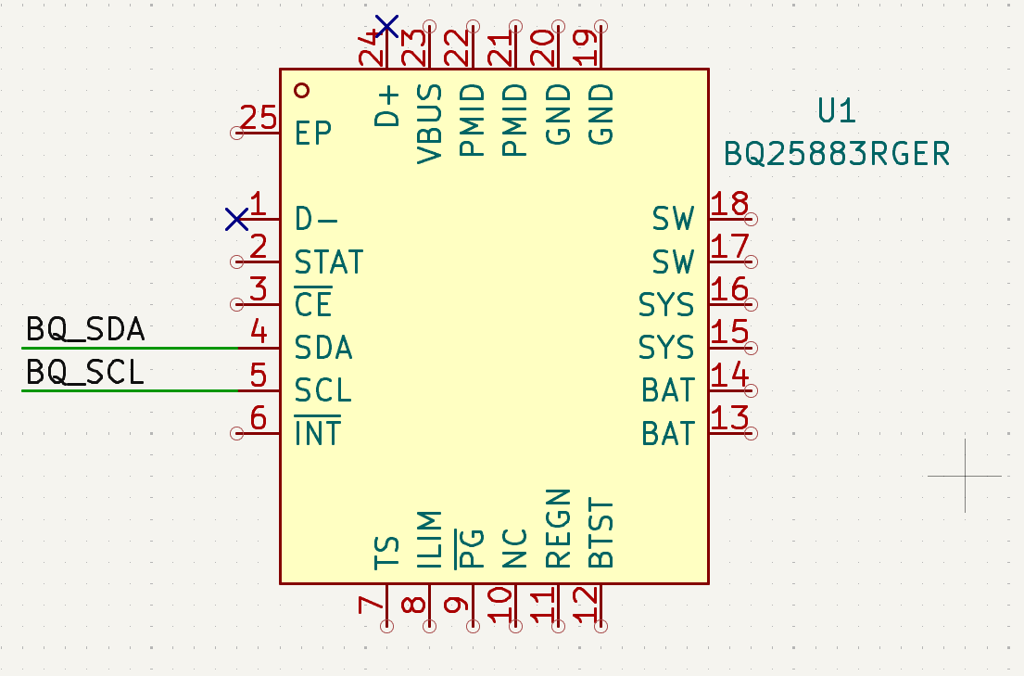
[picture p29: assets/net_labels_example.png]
Net Labels Example


Also, because we are dealing with power, we have to use `separate grounds` such as `power ground` and `digital ground`. Usually, for most chips, we will use the digital ground. However, sometimes we have to work with power components and need to have a cleaner ground reference. In the datasheet, you can see that there are different symbols for ground.

**Digital ground** is used for all the digital components like microcontrollers, sensors, and logic chips. Digital circuits switch on and off rapidly, creating noise on the ground plane. This is fine for digital circuits since they only care about HIGH (1) or LOW (0), not the exact voltage.

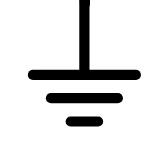
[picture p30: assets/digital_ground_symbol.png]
Digital Ground Symbol


**Power ground** is used for high-current circuits like motor drivers, charging circuits, and voltage regulators. These circuits can draw lots of current, creating voltage drops and noise in the ground connections. Keeping them separate prevents this noise from affecting sensitive circuits.

Power Ground Symbol

#### Why Separate Them?

The noise from digital switching or high-current power circuits can interfere with sensitive analog measurements from the sensors.

The trick is to keep these grounds separate on the PCB traces but connect them together at a single point. The datasheet says to connect them below the `thermal pad` (a conductive area under ICs to dissipate heat/reduce noise) of the chip. This gives each type of circuit its own clean ground reference while still maintaining a common ground for the entire board.

Now wire up the rest of the schematic, and you should end up with something similar to this:

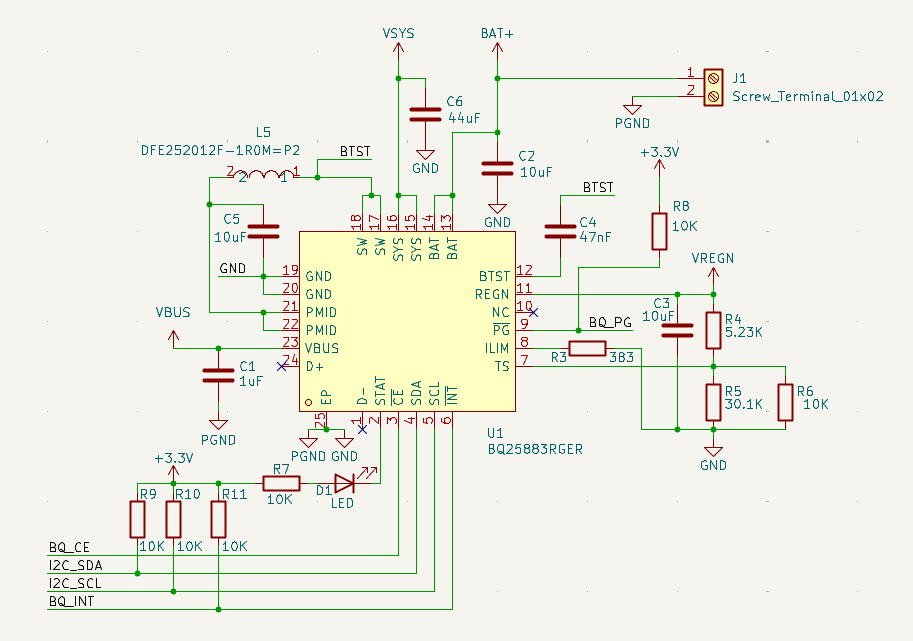
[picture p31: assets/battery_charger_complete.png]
Battery Charger Schematic Complete


Note the mess, but I have different ground names for PGND and GND, although I used the same symbol. I added a battery screw terminal and also connected the battery ground to PGND, and I also shorted PGND and GND. I plan on connecting PGND and GND on the bottom of the thermal pad (this is actually the EP/Pin 25, but in the end I removed PGND and used only GND for simplicity).

### Regulators

Now after finishing the battery charger, I am going to start wiring up the regulators, starting with the `TPS63070`.

Apply the same methodology as wiring up the battery charger: look up the datasheet, go to the `Application and Implementation` section, and look at the schematic. In this case, there are 2 schematics:

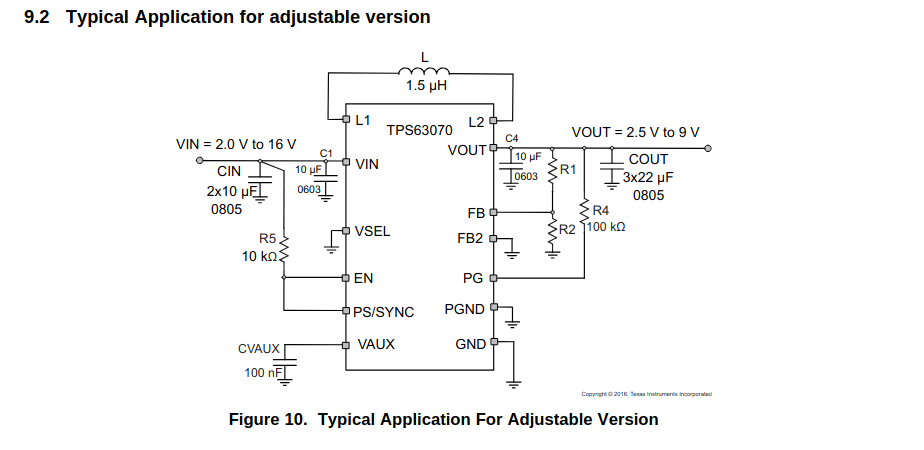
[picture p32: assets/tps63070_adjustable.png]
TPS63070 Adjustable Application

A typical application that can be adjusted depending on your needs.

And if you scroll down a bit more:
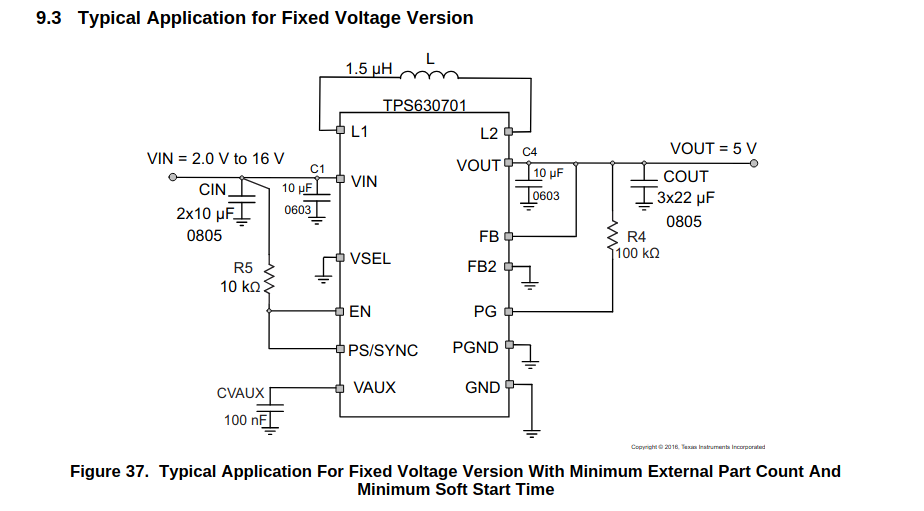
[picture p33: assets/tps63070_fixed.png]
TPS63070 Fixed Voltage Application


Another typical application, but this time it outputs a fixed voltage.

Really, the only difference is that for the adjustable version, there's a `voltage divider`—a pair of resistors that can be used to create a voltage less than or equal to the input voltage:

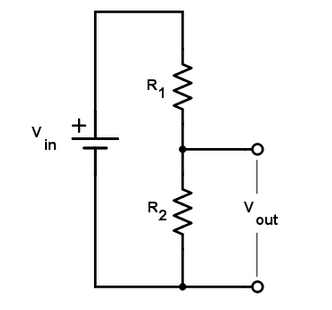
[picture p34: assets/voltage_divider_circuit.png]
Voltage Divider Circuit


In the fixed version, we don't use a voltage divider so it stays at 5V (it's predetermined in the chip).

In our case, we are going to use the fixed version as it uses fewer components and also gives us the 5V that we need.

## TIP

When wiring things based on schematics, make sure to use the recommended size capacitor/inductor values (if mentioned) and set it in KiCad like so when you are going to place the part:
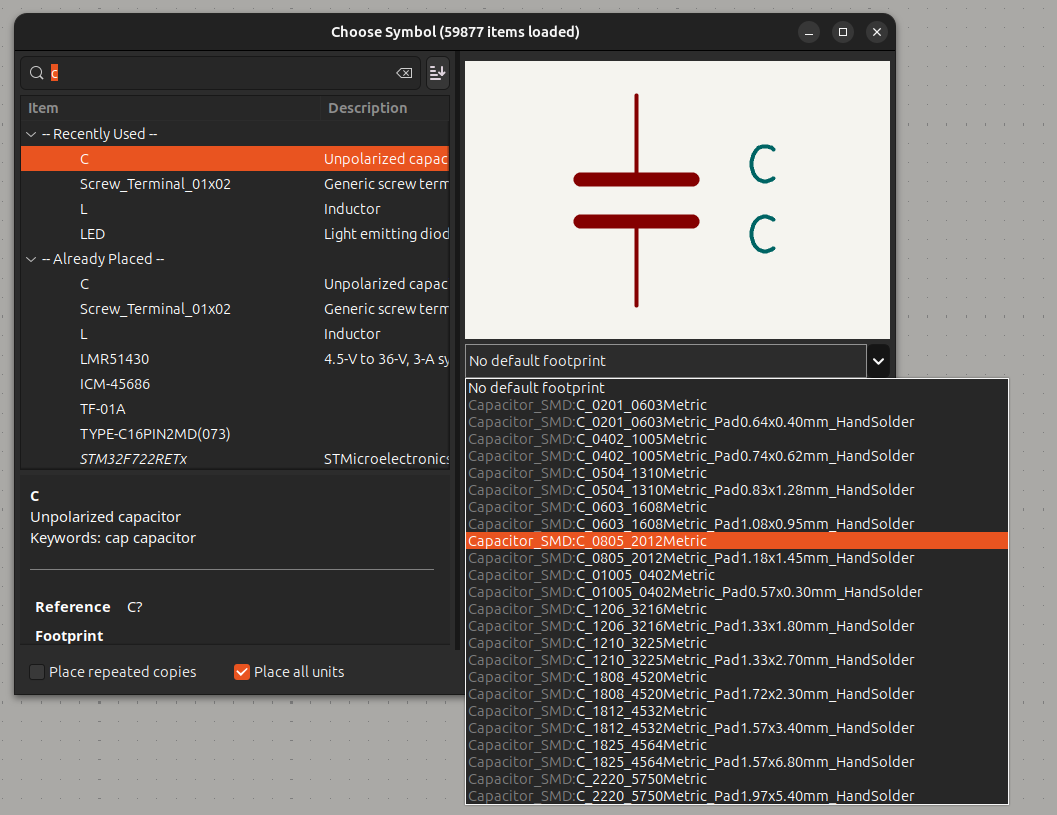
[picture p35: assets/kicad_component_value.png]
KiCad Component Value Setting


---

Using the fixed schematic (and taking into account the correct footprint sizes), wire it up in KiCad. You should get something like this:

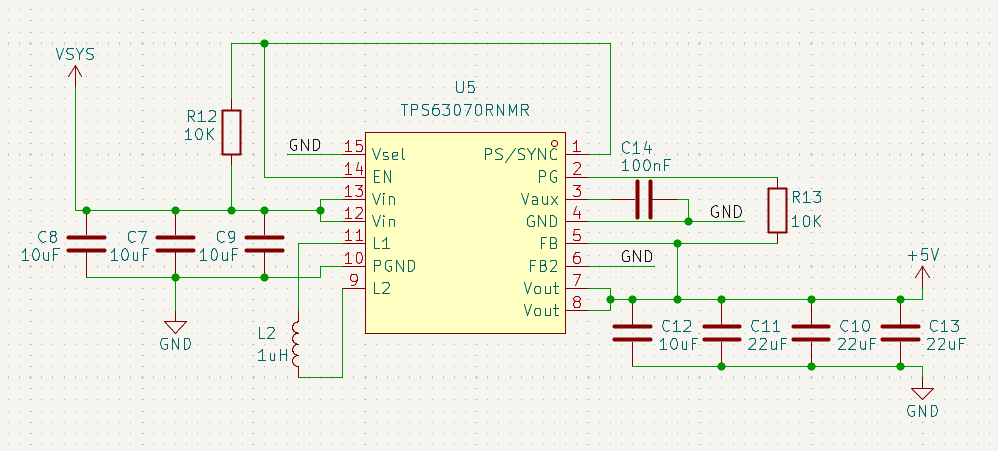
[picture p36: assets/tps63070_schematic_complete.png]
TPS63070 Schematic Complete


With VIN connecting to VSYS (battery or USB voltage) and VOUT connecting to +5V. Separate grounds are not needed here, so they are GND.

If you don't know what footprint size to add to the other components (resistors, inductors, etc.), don't worry. We will revise this later.

Now moving on to the final power part, the `LMR51430`.

Repeat the same as the other 2 parts: open the datasheet and look for the `Application and Implementation` section. Switching regulators (like the name implies) switch MOSFETs (tiny gates) open and close very fast in order to regulate voltage. This can be measured by the `switching frequency` of the chip. In this case, we have 2 tables under the schematic.

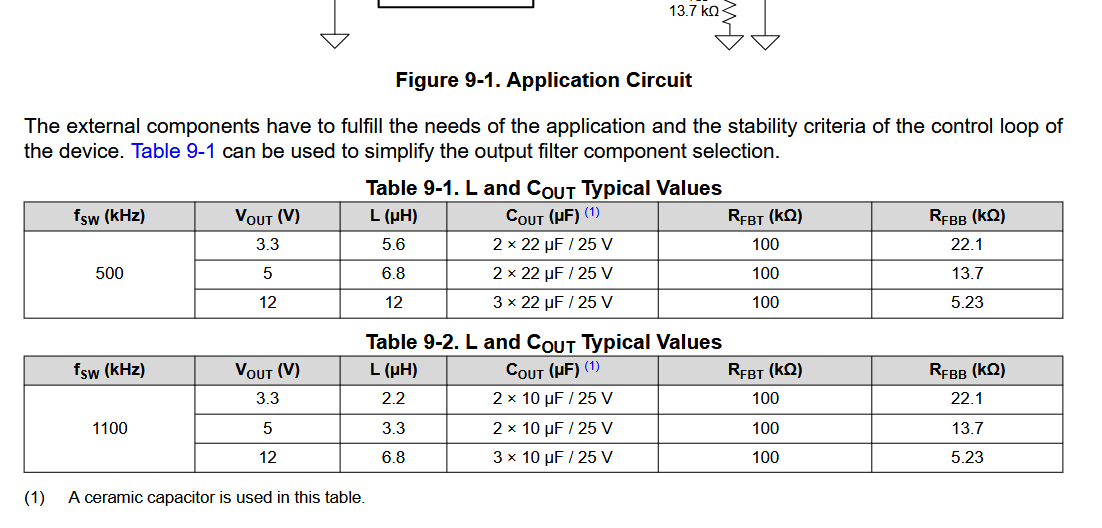
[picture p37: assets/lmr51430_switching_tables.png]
LMR51430 Switching Frequency Tables


One for a switching frequency of 500 kHz and another one for 1.1 MHz (1100 kHz). With a higher switching frequency, it is less efficient and also can produce more heat. However, overall, the space it takes up is less than with the lower frequency. On the other hand, a lower switching frequency is more stable/efficient and doesn't heat up as fast. It also produces a lot less noise (which is what we need). So in this case, we will go with the lower switching frequency at 3.3V. If you want to wire it up based on the higher frequency, then feel free to do so. Just take into account the pros and cons of each one. (All of this information is from the datasheet, by the way.)

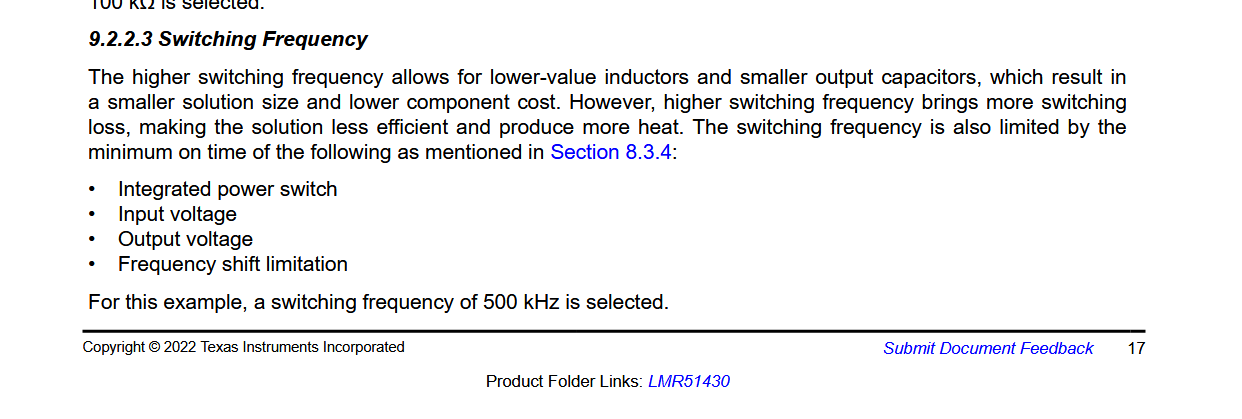
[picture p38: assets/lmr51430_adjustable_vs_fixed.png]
LMR51430 Adjustable vs Fixed Schematic


After routing it, you should get something like this (for a 500 kHz switching frequency at 3.3V):

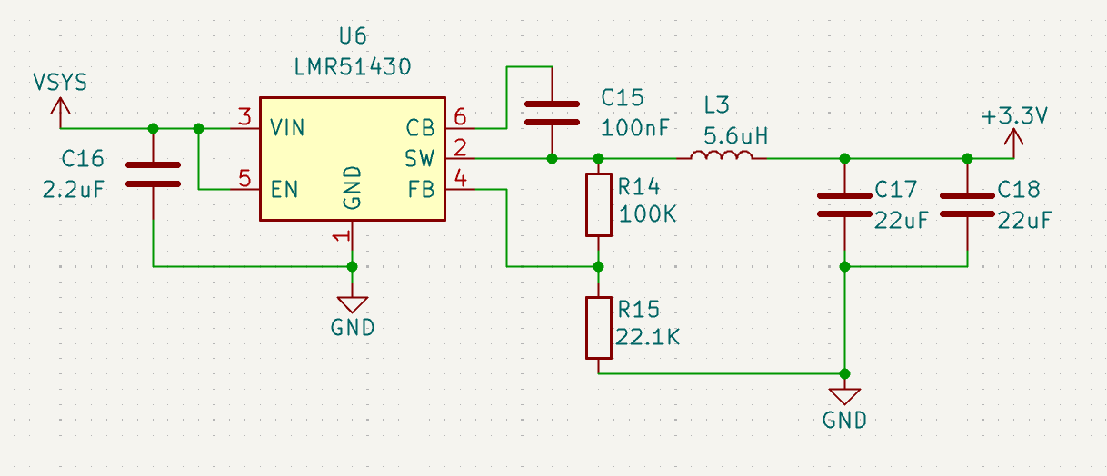
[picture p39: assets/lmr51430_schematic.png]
LMR51430 Schematic Complete


Like the 5V regulator, VIN = VSYS, but VOUT = +3.3V as this chip is giving us 3.3V output.

Double-check the values on the resistor divider as that is what determines the output voltage. Also, in the reference schematic, it shows one capacitor of 44 µF, but in the table, it's 2 capacitors of 22 µF, so I used those.

## Sensors and Peripherals

Now that we've got power out of the way, it's time to route the sensors and the microSD.

### BMP580

Starting with the BMP580, when I try to open the datasheet, it says that no datasheet is defined. So you have to look it up on Google and found [this](https://cdn-shop.adafruit.com/product-files/6411/BMP580.pdf).

Looking around the table of contents, there is no `Application and Implementation` section, but there is a `Pinout and Connection Diagrams` which is close enough:

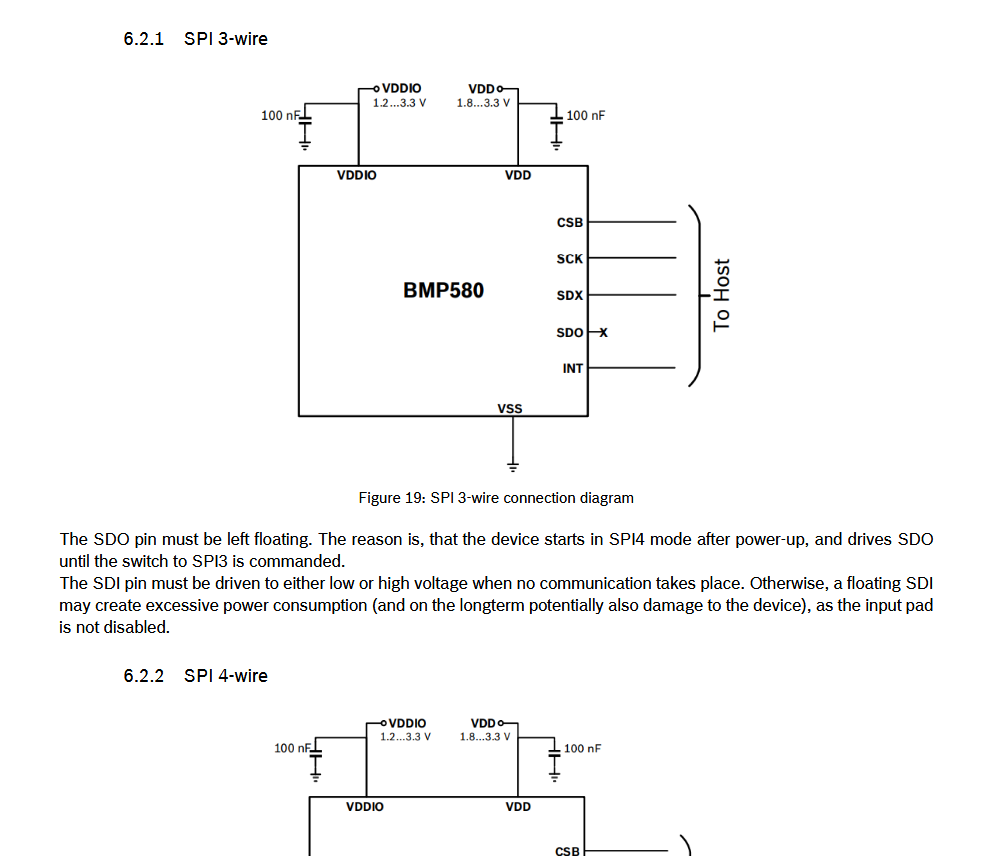
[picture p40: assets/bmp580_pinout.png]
BMP580 Pinout Diagram


Taking a look at the different schematics, there are different ways of connecting the chip through `SPI`, `I2C`, and `I3C`. Above in the **Communication Protocols** section, I explained what each of these mean. For this chip, I plan on using `I2C` as it's the default mode of communication for this chip. (This is personal preference; feel free to use whichever mode of communication you wish.)

When implementing `I2C`, you need to have pull-up resistors on each line. However, if you recall, the battery charging circuit uses I2C as well, and we already put pull-up resistors there, so it isn't necessary to add them here.

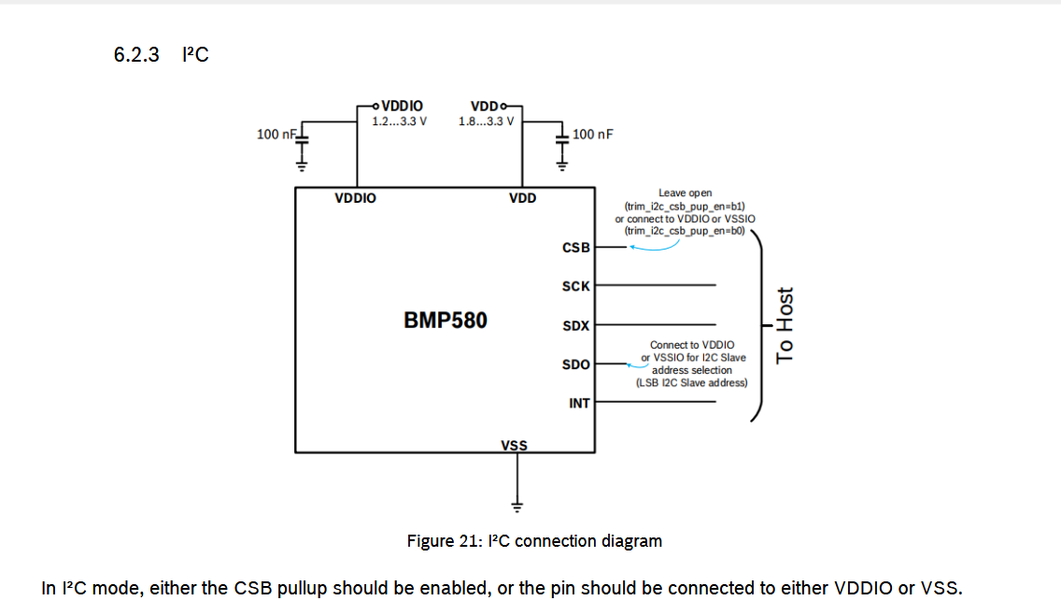
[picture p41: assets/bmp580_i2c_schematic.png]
BMP580 I2C Schematic


Following this schematic, after wiring it up in KiCad, you should get this:

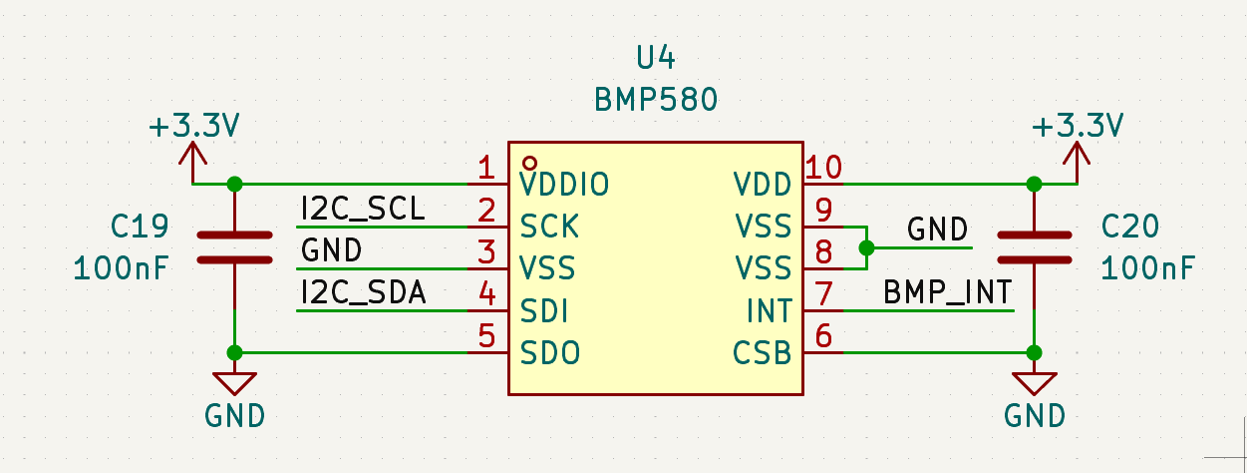
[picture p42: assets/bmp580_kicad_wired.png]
BMP580 KiCad Wired


I wired both VDD and VDDIO to 3.3V as that is the voltage that all of the other chips are running at (microcontroller and sensors).

### ICM-45686

Looking at the `ICM-45686` [datasheet](https://invensense.tdk.com/wp-content/uploads/documentation/DS-000577_ICM-45686.pdf), it has different modes of operation like the BMP580. However, the one that interests us is this one:

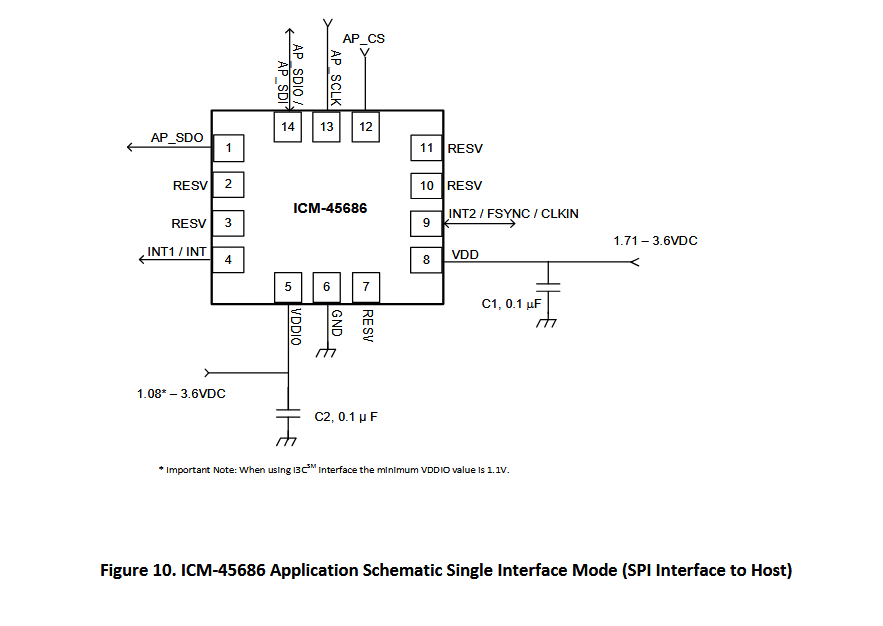
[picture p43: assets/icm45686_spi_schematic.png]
ICM-45686 SPI Schematic


Changing things up a bit, we are going to connect the sensors to the microcontroller through SPI. This gives us the advantage of faster data and also allows us to learn how to implement it later on in code.

Also, in the schematic, looking at pin 14, it serves the dual purpose of being a SDIO or SDI. However, in our case, we want to use it as SDI to use the full capacity of SPI.

You should end up with something like this after:

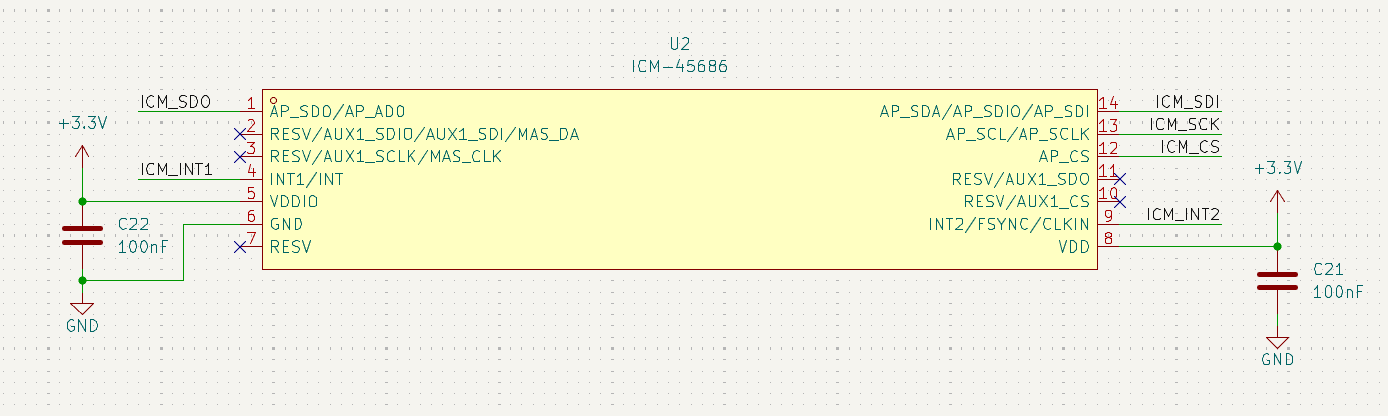
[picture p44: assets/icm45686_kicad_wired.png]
ICM-45686 KiCad Wired


### MicroSD Card

MicroSD works on the same principle as SPI but can have more channels for faster data throughput. This form of communication is called SDIO (Secure Digital Input Output) and can work in 1-bit or 4-bit data modes (4-bit has more channels and faster data transfers).

Here is an example schematic of how the SD card should be wired, but we are going to modify it a bit to fit our needs. There are 8 pins on the microSD, and here's a table showing their meaning:

MicroSD Pinout Table

In SDIO (SDMMC) mode, DAT0-3 are used for data transfer, CLK for clock, and CMD for sending/receiving commands between the microcontroller and microSD card. DAT3 can also be considered a CD (Card Detect) pin, but usually, there is a 9th pin on most symbols that uses the case directly to detect if there is an SD card or not.

Another thing to keep in mind when wiring up the microSD card: **10K PULL-UPS ARE REQUIRED FOR EVERY PIN ON THE MICROSD CARD** (excluding the 9th pin/GND/VCC).

MicroSD Pullup Requirements

After wiring it up, you should get something like this:

MicroSD KiCad Wired

Now all that's left is to connect everything to the microcontroller!

# Microcontroller Break

Since we are using an STM32, there is a really cool piece of software called STM32CubeMX. It basically allows you to select the functions and types of communication that you need, and it automatically selects the pins so that we don't have to read the datasheet and get stuff wrong.

To start, [download it here](https://www.st.com/en/development-tools/stm32cubemx.html) and wait for it to install.

After installing it and opening it, you should be presented with this screen:

STM32CubeMX Startup Screen

Click on `ACCESS TO MCU SELECTOR` as we are going to create a new project based on the MCU that we are using: in this case, `STM32F722RET`.

After searching for the MCU, you should see this screen:

STM32CubeMX MCU Selector

Here, it shows different variations of that version for the STM32, but we are going to select the `STM32F722RET6` version as it is the one that has the most in stock on LCSC.

STM32F722RET6 Selected

After that, hit "Start Project" at the top. If any windows pop up, say yes.

After loading/downloading the firmware, you should be greeted with this window:

STM32CubeMX Pinout Configuration

This is where you will be configuring the pinout for the STM32. On the left, you can see the different sections that are able to be configured. However, the only ones that concern us for now are the `System Core`, `Timers`, and `Connectivity` sections.

## Connectivity

Here, we can see the different ways that we can connect the STM32 to different peripherals through `I2C`, `SPI`, `UART`, `SDMMC`, `USB_OTG_FS`, and more. For now, enable the first I2C channel. This will be for the battery charger and pressure sensor. It should look like this:

STM32CubeMX I2C Enabled

Also, be sure to select pins on either side for the battery charger interrupt and chip enable pins. The BQ_INT pin should be set as a GPIO_EXTIx (x is any number) pin as this lets the STM32 know that this pin is going to be an interrupt pin.

STM32CubeMX BQ_INT GPIO Configuration

For BQ_CE, make sure that there's a pin set to GPIO_Output. According to the datasheet, when the pin is low, charging is on, and when it's high, the battery doesn't charge. We can change this later in the code for further customization in case you don't want the battery charge controller running during flight.

STM32CubeMX BQ_CE GPIO Configuration

**MAKE SURE TO ADD THE INTERRUPT PIN FOR THE BMP580.**

When selecting an interrupt, if it deletes another interrupt, choose another pin as some interrupts use multiple pins.

STM32CubeMX BMP580 Interrupt Configuration

Then enable an SPI channel for the IMU. You are free to use whichever channel you wish, but I am going to select the first one. Select `Full Duplex Master` as the STM32 will be the master and the IMU the slave, and full duplex because we are using both MOSI and MISO and not just one channel for input/output (half duplex/SDIO). There is also an option under the selection to activate a `Hardware NSS Signal`. This is used if we have just one device under the SPI bus and makes it so that the STM32 manages the `Chip Select` pin instead of us having to select a GPIO for it. I enabled it as `Hardware NSS Signal Output` as the IMU will be the input. After selecting SPI, it should look like this (it can be different if you want to use a different pin for the Chip Select):

STM32CubeMX SPI Configured

Also, don't forget to add the 2 interrupt pins on the IMU as GPIO_EXTIx (x is any number):

STM32CubeMX IMU Interrupts

After you've done that, it's time to select `USB_OTG_FS`. This means USB On-The-Go Full Speed, and it differs from `USB_OTG_HS` (USB On-The-Go High Speed) as it is slower and doesn't need any extra pins to configure. It's sufficient for our needs of flashing and sending serial data. Set it to host or device (you'll be changing this later depending on your needs). For now, I will leave it as host, and it shows where the USB pins are on the chip.

STM32CubeMX USB OTG Configuration

Now enable `SDMMC` as this is the communication protocol that we will be using to write/read to our microSD. This should be enabled and set to a 4-bit bus.

STM32CubeMX SDMMC Enabled

Also, remember to add an extra pin next to it for the card detect pin and make it a GPIO_Input:

STM32CubeMX SDMMC Card Detect

Now that we are done with our peripherals/sensors, we are going to configure some other stuff that would be important in starting the STM32 and configuring the servos.

Go to the `System Core` tab, then click on `RCC`, and set both the high-speed clock and low-speed clock as a crystal/ceramic resonator. By doing this, we are telling the STM32 that we will have some external clocks that it can use to achieve faster/stable clock timing throughout the entire chip. We will edit this in KiCad later along with the pins.

STM32CubeMX RCC Configuration

Now go to the `Timers` section. Here is where we can edit the PWM pins for the servos. Select any timer that has channels that support PWM and select 2 `PWM Generation CH` channels. We will be able to edit the **duty cycle** later in the firmware. Also edit the `Clock Source` and set it to the internal clock. This is needed for the PWM generation as it needs a clock to time the signals correctly.

STM32CubeMX PWM Configuration

**MAKE SURE TO SAVE USING CTRL+S AND CREATE A NEW FOLDER IN THE ROOT OF YOUR GITHUB REPOSITORY CALLED `software` OR `firmware`.**

STM32CubeMX Save Location

This is how my STM32 looks after selecting all of the pins:

STM32CubeMX Final Pinout 1
STM32CubeMX Final Pinout 2
STM32CubeMX Final Pinout 3

Keep this open while we configure the rest of the microcontroller in KiCad.

# Back to KiCad

Now after adding all of the pins and peripherals and knowing which pins you are going to use, we are going to finish wiring up the STM32 with what's called a `reference schematic`. If you want to learn more about this specific type of chip or any STM32 MCU in general, there is a documentation tab ([example](https://www.st.com/en/microcontrollers-microprocessors/stm32f722re.html#documentation)) that shows you all the implementations/peripherals that you can have with the STM32. After scrolling around, I found a [reference design](https://www.st.com/resource/en/application_note/an4661-getting-started-with-stm32f7-series-mcu-hardware-development-stmicroelectronics.pdf) to use with our STM32.

Going to the section named `Reference Design`, we are greeted with this:

STM32 Reference Schematic

## Wiring up Power

Starting with the `decoupling capacitors` (capacitors that are placed near ICs to stabilize voltage on power supply lines—they are in parallel with voltage and connect to ground), it is generally good practice to place one **100 nF** per VDD pin and then use a bigger **1 µF** capacitor per section (e.g., VDD/VDDA/VBAT). Finally, finish off with a big **4.7 µF** or **10 µF** capacitor on the main voltage line before the STM32 to handle larger voltage spikes. If you have analog voltage (VDDA), it's also good practice to put a `ferrite bead` (like a capacitor, but it suppresses high-frequency noise currents) before connecting it to VCC to prevent noise from digital switching from interfering with sensitive analog functions.

It is also needed to place a 2.2 µF capacitor in series with VCAP and GND.

**VERY IMPORTANT: PUT A 2.2 µF DECOUPLING CAPACITOR ON EACH VCAP PIN OF THE STM32 OR IT WON'T BOOT UP.** (From experience)

Based on this information (and the schematic), try to wire up your STM32's VDD/VSS pins (VSS is GND, by the way). You should get something like this:

STM32 VDD/VSS Wiring

I placed the capacitors off to the side to make it look cleaner, but it's the same as if you were to connect them directly. Just make sure that when you are placing/routing them on the PCB, they are **AS CLOSE AS POSSIBLE TO THE PIN THAT THEY ARE DECOUPLING OR IT DEFEATS THE PURPOSE.**

## Clocks

Looking at the reference design above, it shows that we need some buttons for the reset and boot pins. These buttons allow us to restart the MCU and allow it to boot into its bootloader to allow for programming through USB.

We also have to add the 32.768 kHz and 25 MHz clocks mentioned in the datasheet. These clocks are important for PWM and other functionality that requires timing that you may want to add.

I am going to import all of these parts from LCSC using the script that we used before (including the ferrite bead). Here are the updated part numbers:

- C720477 (Button)
- C9006 (25 MHz Crystal)
- C32346 (32.768 kHz Crystal)
- C141723 (Ferrite Bead)

After running the script, import all of the parts in. I replaced the ferrite bead with the part from LCSC:

KiCad Crystal Imports

Now it's time to place the crystals. These crystal oscillators use a `piezoelectric` (ability of certain materials to generate an electric charge when subjected to mechanical stress, and conversely, to deform when an electric field is applied to them) `crystal` to generate a stable and accurate frequency reference signal. When using these crystals, you need to place `load capacitors`:

Crystal Load Capacitors Concept

Think of the crystal like a kid on a swing. It is going back and forth at a certain oscillation. The `load capacitors` would be weights that you add onto the swing to speed it up or slow it down to get the exact frequency. The same applies to the crystal oscillators. The capacitors are used to fine-tune the oscillations (clock speed) of the crystal.

Each crystal has a datasheet that specifies the load capacitance that it needs, and I have already looked them up for the crystals mentioned above. **REMEMBER THAT EACH CRYSTAL IS DIFFERENT EVEN IF THEY MIGHT HAVE THE SAME FREQUENCY.**

The capacitors for the 25 MHz crystal should be 20 pF and for the 32 kHz should be 6.8 pF. After you're done adding them, it should look like this:
KiCad Crystals Wired

## Buttons

Now for the reset and boot buttons. These are super important for flashing or working with your STM32 in general. Taking a look at the reference design above, we need to connect the reset pin to a button parallel with a capacitor to ground. For the boot pin, we need to create a button that will set the boot pin to 3.3V when we press it. (Look at the datasheet to learn more.) This allows us to change the boot configuration depending on whether the boot pin is a 1 or a 0. In the end, it should look something like this:

KiCad Reset and Boot Buttons

## Servo Headers

Almost done, just need to add in some 3-pin headers to control the servos. They typically have a pinout of 5V - PWM - GND so it's good to keep the pinout in that same order. Mine looks like this in the end:

KiCad Servo Headers

# Finish Schematic

Now all that's left to do is to finish the schematic by adding net labels on all of the pins that we have used in STM32CubeMX. Your layout might look different from my layout if you're using a different chip or sensors, but here's how my STM32 looks after adding all of the net labels:

KiCad Net Labels Schematic

For the USB lines, DM = DN, and DP = DP.

For the ICM SPI lines, SDI = MOSI. (For the ICM, it's an input, so it would be MOSI (Master Out Slave In) for the STM32.) By that logic, SDO = MISO.

Note that for the I2C lines, I changed the names to be able to connect to each of the devices like so:

KiCad I2C Connections 1
KiCad I2C Connections 2

You may have a different pinout than me, but as long as you know which pins you are using and for what, then you'll be fine.

**DOUBLE TRIPLE CHECK THAT YOUR PINS MATCH THE ONES IN STM32CUBEMX.**

Now that you're done with your schematic, organize everything so that it looks nice. You might have to change the page settings via `File > Page Settings` in order to change the size of it:

KiCad Page Settings

Now after organizing it a bit, your schematic should look like this:

KiCad Final Schematic

I placed text to name each block and added a title at the bottom right.

**Finally, we're done with the schematic!**

# Footprint Assignment

Before continuing on to the PCB, we have to `Assign Footprints` which basically tells KiCad how big each component is physically and how the connections look in real life to be able to solder it.

Click on this button to open the footprint selection screen:



The lines in yellow are components whose footprints we have to assign:



But since it's mainly resistors and capacitors, that makes it a lot easier.
Since we're designing a flight controller, this has to be as small as possible, so I am going to be choosing the smallest footprints I can (while staying within good practices). The smaller the footprint, the more it can heat up and the less it can tolerate (for resistors and capacitors). A rule of thumb that I go by is any resistors under 80K I assign a 0201 footprint, over that and it's 0402. For capacitors, any `bulk capacitors` (capacitors that have high values like 4.7 µF or 10 µF) I usually assign 0402. Any bigger than 10 µF and I assign 0805, but it depends on the datasheet of the component. Under the application and implementation section there is usually a table that specifies which footprints/components to use.

Now all that's left is to finish adding the footprints for these symbols:



For the LED, I am going to have it in a 0402 package. And for the headers, I am going to use these footprints (basically the standard headers for jumper cables):



The inductors are a bit trickier. For this, you're gonna have to go into the datasheet and see where it says the size:



For that `5.6uH` inductor, I am going to be using `C18236327` (LCSC Part Number).

For the 5V buck-boost, I am going to be using `C3033018`. I also noticed that I had the inductor value wrong from the datasheet. **THIS IS WHY DOUBLE CHECKING IS IMPORTANT:**



For the final inductor in the battery charging IC, I am going to use `C435392`.

Press `Apply, Save Schematic & Continue` to save the footprints you have already placed and then import the new inductors that you have selected.

# PCB Layout

Now go to the PCB section in KiCad. There's a button at the top of the schematic page that says `Switch to PCB Editor` to go there.

Then to import all of our components from the schematic, we hit this button:



A screen should pop up:



There should be no errors or warnings. Then press Update PCB to import everything from the schematic.



Now comes the fun part, part placement!

## But wait, what's a PCB?

A `PCB` (Printed Circuit Board) is a board used to mechanically support and electrically connect electronic components. It is composed of layers of copper and a `dielectric material` (a material that acts as an "insulator" and isn't conductive). PCBs can have from 2-32 layers, although for this board, we will be working with 2 (maybe 4 if we need to).

In KiCad, if you look to the right, it shows the different layers:



`F.Cu` and `B.Cu` (Front Copper and Back Copper) are our copper layers (denoted by the `.Cu`). The only other layers that are important to us are `F/B.Silkscreen` and `Edge.Cuts`. The silkscreen layers allow us to put text/images and is usually that white text that you find on any PCB. `Edge.Cuts` is the layer for the edges of the board (e.g., where JLCPCB will cut to make the outline). For now we will focus on the copper layers and routing. We can add more copper layers later in the board settings.

Now we have to connect each of the components and `route` them (create copper lines between each of them).

## Layout

I personally have always relied on this one trick to route my PCBs and it has always helped me without fail. First, separate the components into their respective groups (e.g., all of the components for the battery charger, 5V regulator, 3.3V regulator, STM, etc.), then lay them out and route them in those groups, finally put the groups together on the PCB and route the connections between them.

Starting with USB-C, go to the schematic and select the USB-C section:



Then going back to the PCB editor, you should see that the connector and its parts are selected. Then drag them off to one side.



Do the same for each of the sections and after you've done that you should get something like this:



Now go section by section and place the components close to where they're supposed to be connected. Make sure to place decoupling capacitors close to the pins that they need to decouple or they won't work.

Example of the USB-C connector:



I placed the resistors close to the pins that they need to decouple and in a good orientation so that I can connect that ground pin easily.

For the 3.3V Buck converter I routed it like this:



But now I'm realizing that the components I chose are too small so I am going to make the capacitors and resistors a bit bigger:



Ignore the silkscreen for now (the yellow) we are going to come back to that later.

Continue on for each of the chips. For example, here is how I placed the 5V buck-boost converter:



As you can see, the capacitors are close to the pin and to each other, and all of the components I have placed in a way where I can create easy connections like so:



Moving on to the battery charger:



Crystals:


microSD Card:



For the STM32/microcontroller, it's a personal preference of mine to rotate it 45 degrees so that it's "easier" (subjectively) to route later. You can change this by editing the `orientation` property:



Also for these decoupling caps:


I changed the sizes to be 0402 as they are bulk decoupling capacitors and should always be a bit bigger than the normal ones.

After laying out the decoupling capacitors for the STM32, it looks like this:



That one capacitor that is by itself on the right is the big 10 µF capacitor that I plan on laying out later depending on where the 3.3V is coming from.

### Final Layout

After you're done laying out all of the `passive components` (resistors, inductors, capacitors, etc.) and their respective ICs, it's time to layout each of those groups on the board.



Here's what my "board" layout is and I'm going to play around with the placement of each of the groups before routing to make it more compact.

**TIP**

It may be helpful to literally group them in KiCad to move them around easier.

After a bit of laying out and thinking I came up with this:



The battery charger is close to VBUS and then VSYS has an easy path through to the 3.3V buck converter and 5V buck-boost. The battery connector is also on that side. On the top is the microSD card with a connection to the STM32 directly under it. On the top left are the buttons for boot and reset and also the 2 clocks. On the bottom left is the IMU that is kept separated from the rest to reduce noise (happened by accident lol) and the STM32 in the middle whose USB DP and DN pins are inline with the USB-C port.

You don't have to use this exact layout but try to have one that's "organized".

Now after defining the layout, go to the `Edge.Cuts` layer and create a rectangle with the tool on the side:



This will be the PCB outline.




When I originally created the board size to cover all of the parts, it had a size of 42.7mm x 47.8 mm so I decided to round it to 40mm x 46mm (optional). After creating the board outline, you may need to shuffle some stuff around for it to fit. It's good practice to put the USB-C connector hanging out a bit so that you have space to plug in the cable like so:



After organizing it, look at the board in the 3D viewer to get a good feel for how the components are going to look. Don't worry if the silkscreen/3D models look terrible for now, we will fix that at the end.





## Routing

Before we start routing, let's configure the `Design Rules`. These are rules that KiCad has to impose certain restrictions like spacing between components and track width and via size, among other things. It is also where we can add default sizes for `vias` (holes that connect tracks between layers) and `tracks` (copper lines that connect components).

Go to the `Pre-defined Sizes` section:


I am going to add `0.6mm`, `0.4mm` and `0.2mm` track widths. For vias, I usually go with vias that have `0.6mm Diameter / 0.3mm Hole` and `0.4 Diameter / 0.2mm Hole`.

Now after that we have to edit the `constraints` of the board so that KiCad doesn't throw an error when we try to place them. Go to the `Board Setup` and then `Constraints`.





Here we are going to change a couple of settings due to the size of our board. We need to be able to place smaller vias and traces, so change the `Minimum via diameter` to `0.4mm` and the `Minimum through hole` to `0.2mm`. After that's done, click OK and you can start routing!

### How to Route

Basically connect each of the pads to their connections and try to use as few vias as possible. I usually try to route the signal stuff (USB, sensors, microSD, crystals, etc.) first and then the power.

(Press x to start routing or use the buttons on the side).

Starting with the USB-C data lines, these are what's known as a `differential pair`, so they have to be the same length as they carry a signal that needs to be in sync with the other and the only way for that to happen is if they're the same length. Start connecting them like so:



Then go to `Route > Route Differential Pair`

and then click on the USB_DP to the far right:

Then route it to the STM32. That's basically the only component that needs differential routing.

Moving on, just some general tips. I personally like to use `0.6mm` or `0.4mm` width for power stuff, mainly anything that runs either 5V (0.6mm) or 3.3V (0.4mm), and you can change the track width or via size from these drop downs at the top.





I also like to do the same as in the layout where I route all of the passive components to their respective ICs before then routing those groups together. For example, routing the decoupling capacitors to the IMU before connecting it to the STM32:

IMU Decoupling Capacitors Routed

You might have to rotate components as well to get a good placement. For vias, I aim to use a maximum of 2 per line like so:

Via Placement Example

Don't worry about connecting the GNDs for now, as we are going to use what's called a `ground plane` (a copper area of GND that can connect to pins/pads).

Sometimes for VBUS on USB-C or any other component, you might have vias that can't pass through, so I added a `0.3mm` track width in the board settings and it works:

VBUS Routing Issue

VBUS Routing Fixed

If KiCad doesn't let you place a via on a pad for whatever reason, you can edit the clearance in `Board Setup > Net Classes`. I set it to 0.15, but try not to set it any lower as the minimum for JLCPCB is `0.1mm`:





This is how I routed the Battery charger:


See how I used wider traces for power lines and thinner traces for the other pins. I plan on wiring the I2C lines and INT pins connecting to the BMP580 like so:



I connected them to the STM32 through the underside to save space (very useful sometimes). Also, I hid the silkscreen layer so that I can route easier.

Then routed the microSD card:



Then finally I routed the 3.3V line, using 0.6mm tracks and then branching off into smaller 0.3mm tracks to connect to the different ICs.

**REMEMBER THAT THE 3.3V MUST GO THROUGH THE DECOUPLING CAPACITORS FIRST BEFORE REACHING THE PIN LIKE SO:**


After routing your board should look something like this:



Now we are going to add the ground pours. This is so that we don't have to manually connect all of the ground pads and it also helps with interference and noise across the board.

Go to the right and click on `Draw filled zones` and click on one corner and a window should pop up:



Here you need to select both layers of copper and select the GND net. Then you need to change the clearance and minimum width to both 0.2mm and also change the `Pad connection` to `Solid` or `Thermal reliefs`. Solid allows the ground plane to connect to the pads better but Thermal reliefs is good if you need to solder/fix the board as the solid ground plane makes it difficult to heat up specific components. For this tutorial I am going to use `Solid` but feel free to use `Thermal reliefs` if you want to be able to solder it later. Press OK and start creating the zone like so:



You want it to look something like this:



Then press `b` on your keyboard and it should fill the zone automatically (`Ctrl-b` to clear them).



Now you should check if you have any `ratlines` (blue lines that signal unconnected pins) and fix them. In my case, I forgot to connect the servos so I will do that now.

Now you need to check if there are any holes that don't have any ground plane and add a `stitching via` (via that connects ground/power planes to cover everything) like so:





You also might see a ratline connecting a piece of the ground plane. This usually means that you need a stitching via in that area.



As you can see, the ground plane connecting to Pin 18 isn't connected to the rest of the ground plane, so we need to add a stitching via there like so:



**SUPER IMPORTANT: FOR ANY COMPONENTS THAT HAVE A THERMAL PAD, CONNECT IT TO GND WITH A STITCHING VIA (depends on the chip but check the datasheet to be sure):**


(You can edit the properties by right clicking the pad and editing the `Net name`.)



Also Notice how I didn't connect the grounds together and connected both PGND and GND, that was made automatically by KiCad when I connected the EP Pin of the battery charger:



After connecting everything we are going to run `Check DRC` which basically checks the design rules and makes sure our board is ready for production.



Then click on `Run DRC`:





Unselect the warnings and look at the errors. If there are any errors about unconnected pads then you should probably go back and make sure that everything is connected. There are some errors but those are from the parts that we imported like the USB-C and microSD card that KiCad is complaining about the holes:



Those errors are safe to ignore but any others you should probably fix.

And with that out of the way, congrats! You've finished the PCB!

Now all that's left is to add silkscreen and make it look pretty and then get the files ready so you can order it on JLCPCB (or any other board manufacturer).

# Finishing Touches

Now I'm going to fix the silkscreen component names so that they look better (and a bit smaller). Go to `Edit > Text & Graphics Properties`



This window should show up:


Here you're going to select `Reference designators` as this will select all of the designators (R1, C1, etc...) on the board so we can edit their properties. Then in the action I am going to change the font and the size:



You can set these values to whatever you want but I am going to go with this. Then click `Apply` to test it out and `Apply and Close` when you are done.

Now all I'm going to do is organize the references like this:


(before)

(after)

This is completely optional but look at how neat it looks now with all the designators/references properly sized and placed:



I even added text to the battery connector to show which side is + and -.

If you want to add the 3D models to render, then just go to properties and find a 3D model that works for you:



(You may have to click on the folder icon next to the path/show button to change the 3D model from a `.wrl` to the `.step` in the same folder for imported LCSC parts for it to show. Just changing the name will not update it.)

3D Model Before
(Before)

3D Model After
(After)

And you're done!



# Exporting Production Files

To get your project ready for submission, we need to export the production files (gerbers, etc.). These files tell JLCPCB or whatever board manufacturer how to make the board and which components to place.



Thankfully, there's a plugin that KiCad has to make this export easy. Go to the `Plugin and Content Manager` in KiCad and search for `jlc`.

You should see this plugin show up:



Press the install button and then `Apply Pending Changes` to install it. Finally, go back to your PCB screen and you should see this icon:



A window should open and click `Generate`:



It should create this directory in the `hardware` folder:



But I'm going to copy it out of that folder and move it to the root so that reviewing is much easier.



Now open [JLCPCB](https://jlcpcb.com/) and upload the gerbers (ZIP file that has the name of the KiCad project) in the `production` folder to see how much it costs.



Select `PCBA` and make sure that it is only one side and that you order 2 and not 5 boards assembled to minimize cost:



Continue and upload the `BOM and CPL` (BOM = bom.csv, basically the components and their ID; CPL = positions.csv, where exactly the components are placed):



Depending on the sensors you use, you may have to use standard PCBA:



If there are any components that have shortfall, then you need to order them separately and add them to your library before ordering:





Continue without placing the parts for now to get the general cost of the board:



**CONGRATS! YOU'VE MADE YOUR FIRST FLIGHT CONTROLLER!**

Feel free to modify this board to include more sensors, servos, peripherals, microSD cards (lmao), literally anything you can put your mind to.

# Firmware

Now you can either write your firmware through STM32CubeMX/VSCode or use [STM32duino](https://github.com/stm32duino/Arduino_Core_STM32).

## STM32CubeMX

After you have received your board, you need to write the firmware to communicate with the STM32. From STM32CubeMX, go to the `Project Manager` section, then click on `Toolchain / IDE` and select `Makefile`. This allows you to use `VSCode` or any other code editor to edit the files much more easily without having to use ST's software.

STM32CubeMX Toolchain Makefile

Now click the `Generate Code` button at the top and download/install any packages that are required.

After that's done, open `VSCode` and open the `software` directory. You're also going to want to install this extension to make building the software much easier:

VSCode STM32 Extension

Then you should see this button on the side:
VSCode STM32 Sidebar Button

This will allow you to build and flash your flight controller all from VSCode!

VSCode STM32 Build and Flash

If you need to edit the pinout or functions of any pin, remember to generate the code again from STM32CubeMX.

Edit `main.c` and remember to keep your code inside the commented sections that say `USER CODE BEGIN` and `USER CODE END` to prevent it from being overwritten when you generate the code again. There are many tutorials online/on YouTube on how to program with STM32, so I'd recommend looking there. You will also need files called `drivers` to control each of the chips/sensors that you use, but those can be found on the internet/GitHub and can be imported into your project easily. ([example](https://youtu.be/dnfuNT1dPiM?t=1343))

## STM32duino

Follow the instructions in the [GitHub](https://github.com/stm32duino/Arduino_Core_STM32#getting-started)

---

If you have any questions feel free to DM me on Slack (@NotARoomba) and if you want to check out my other projects, here's my [GitHub](https://github.com/notaroomba) / [Website](https://notaroomba.dev).

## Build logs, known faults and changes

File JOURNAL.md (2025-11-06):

<!--
  ===================    !!READ THIS NOTICE!!   ====================
  DO NOT edit this file manually. Your changes WILL BE OVERWRITTEN!
  This journal is auto generated and updated by Hack Club Blueprint.
  To edit this file, please edit your journal entries on Blueprint.
  ==================================================================
-->

## 10/26/2025 - Started Guide and Schematic  

I started writing the guide, it is over 400 lines with images and I have also been writing step by step how everything works from the ground so that anyone who reads it can kind of understand the different concepts that there are in advanced PCB design. 

I then started the schematic and just finished routing the battery charger and also the USB-C port.



## 11/2/2025 - Finished the schematic  

I finally finished the schematic and tutorial up to that part. I had to read through the datasheets and wire each component and then update the guide explaining everything in detail. I also added a section explaining STM32CubeMX and how to configure it and get all of the pins set up.



## 11/5/2025 - Finished the guide  

I explained how to add footprints, how to place components on the PCB, and also how to route. I took a lot of images and here's how the board turned out:



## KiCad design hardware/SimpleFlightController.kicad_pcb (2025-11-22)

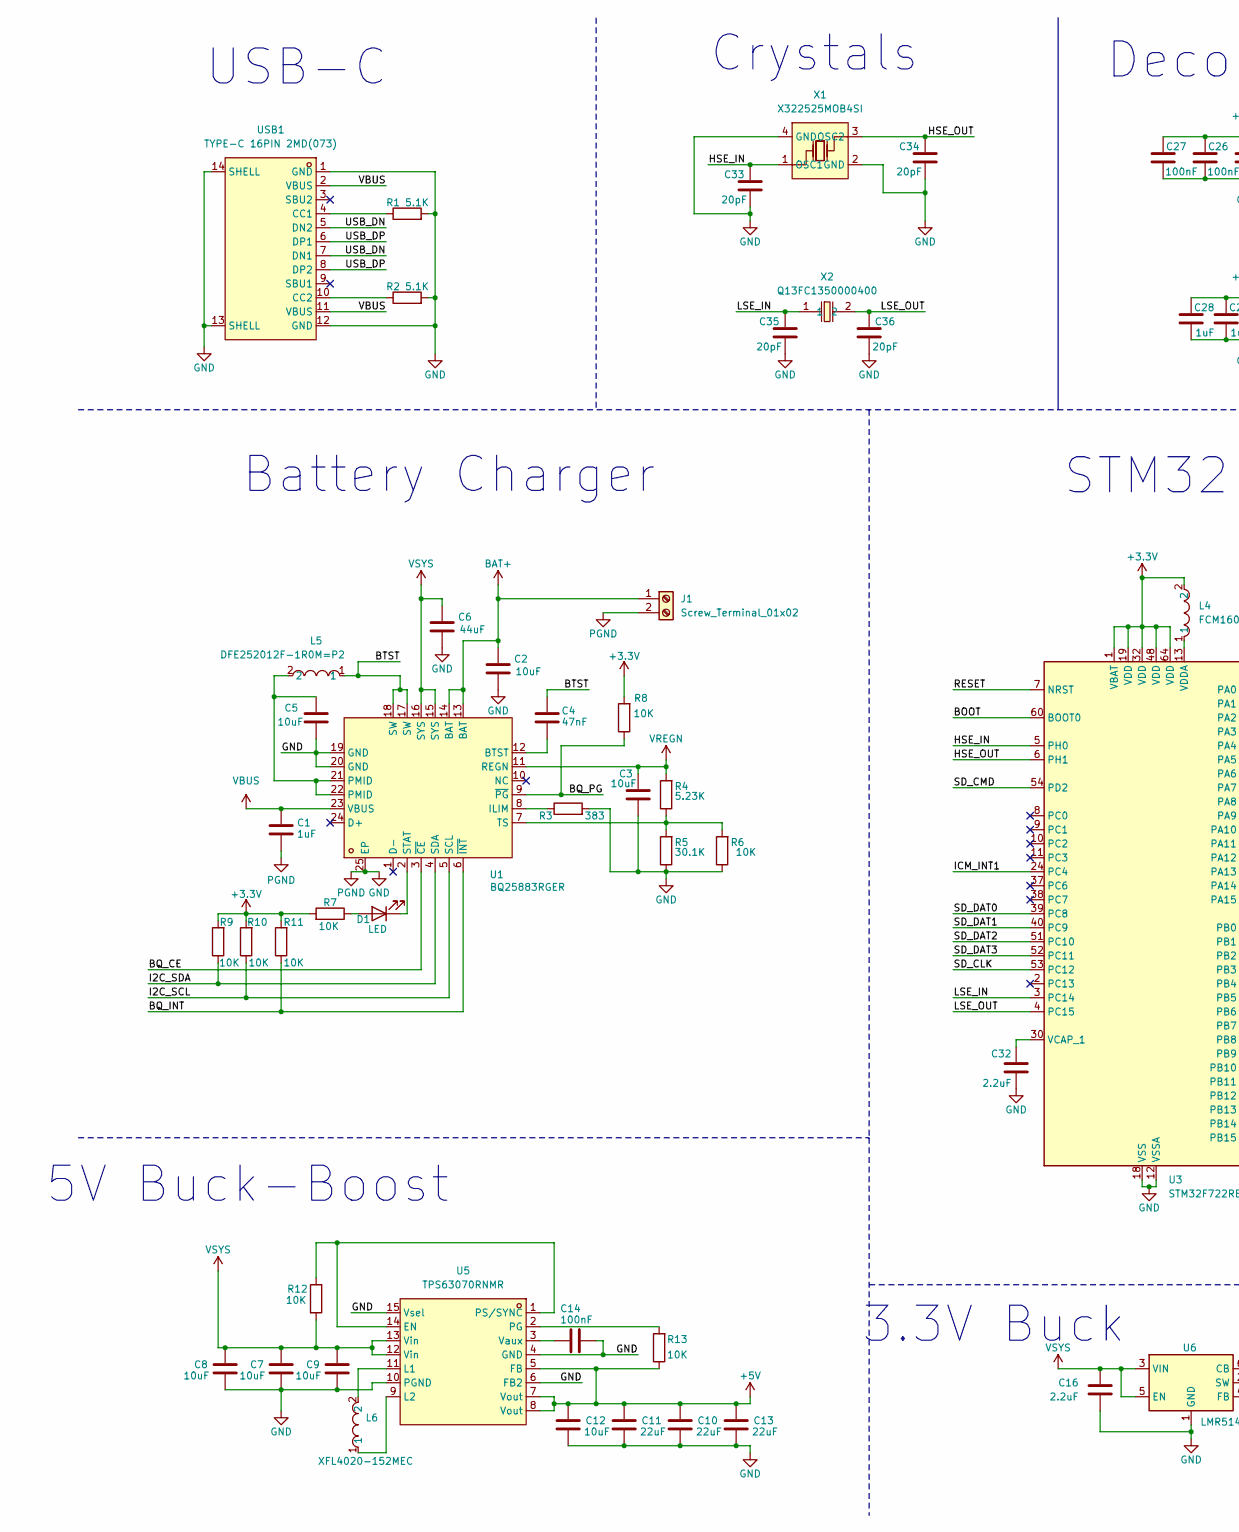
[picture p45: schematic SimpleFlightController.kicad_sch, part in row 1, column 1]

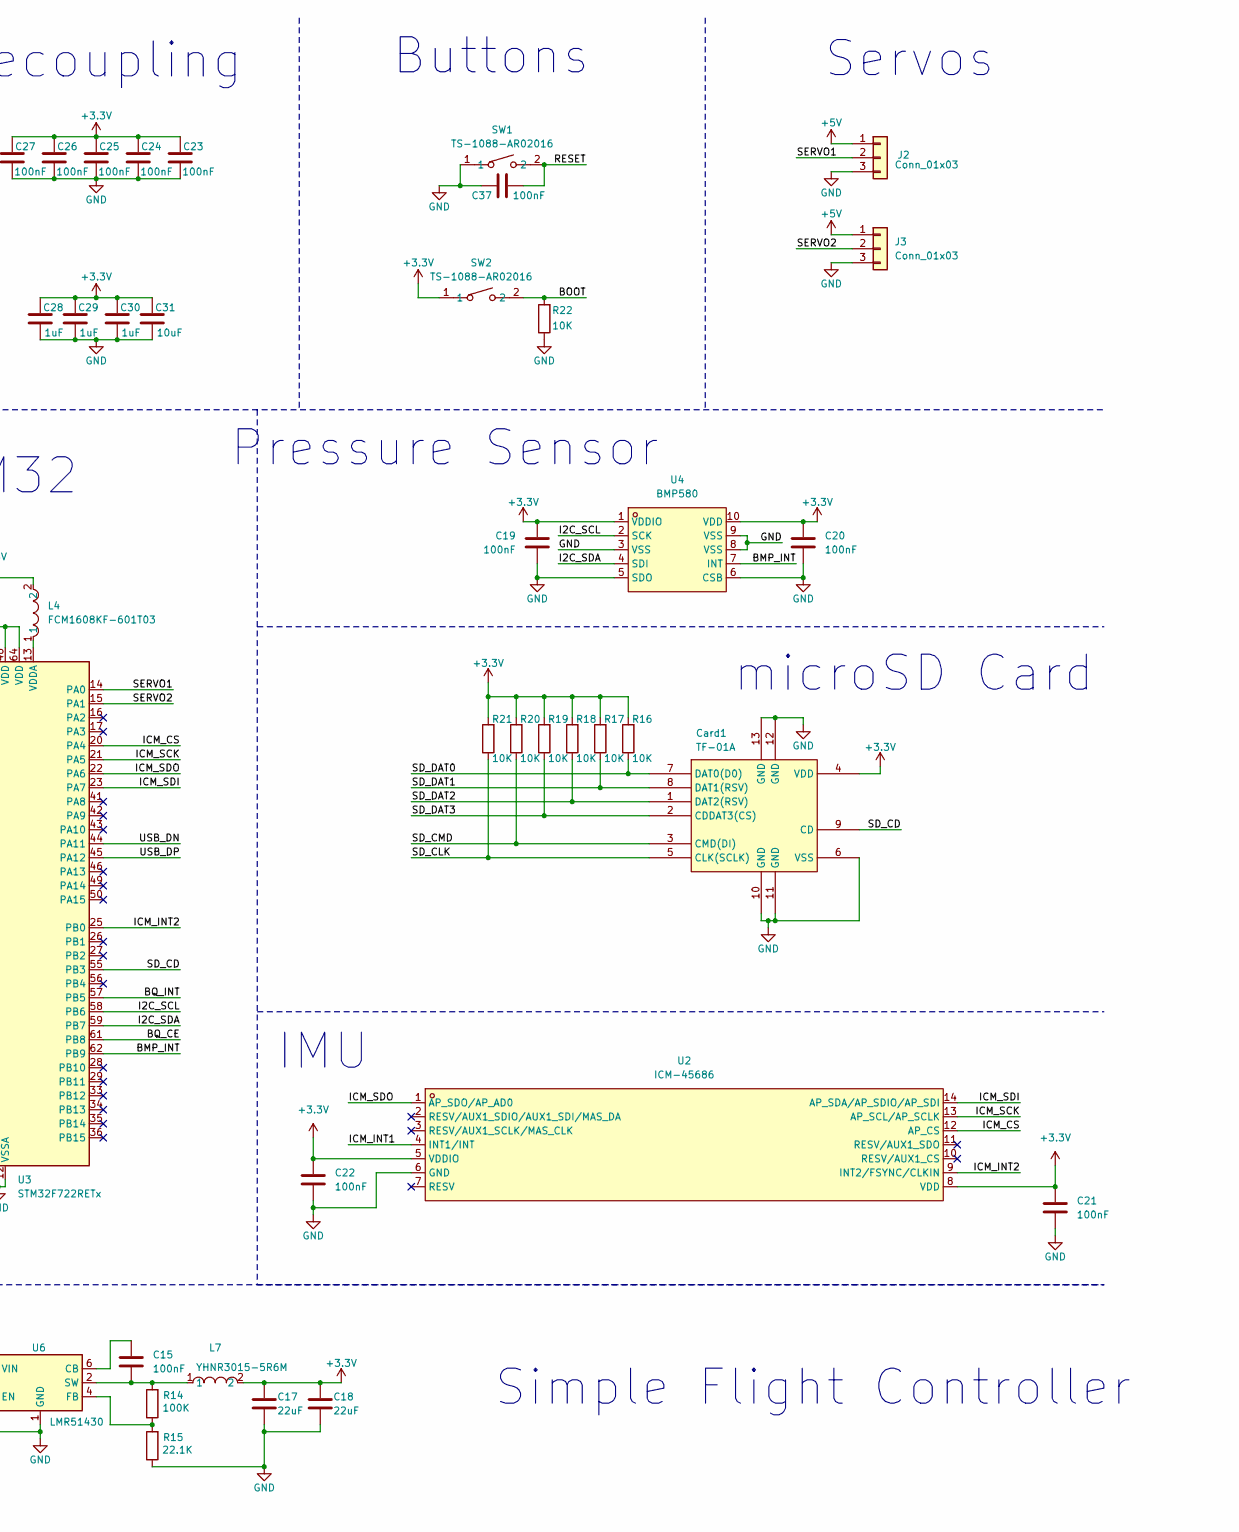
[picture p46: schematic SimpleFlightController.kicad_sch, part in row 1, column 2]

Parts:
C1, C28, C29, C30: 1uF; C_0402_1005Metric
C2, C9, C12: 10uF; C_0603_1608Metric
C3, C5, C31: 10uF; C_0402_1005Metric
C4: 47nF; C_0201_0603Metric
C6: 44uF; C_0603_1608Metric
C7, C8: 10uF; C_0805_2012Metric
C10, C11, C13: 22uF; C_0805_2012Metric
C14, C15, C19, C20, C21, C22, C23, C24, C25, C26, C27, C37: 100nF; C_0201_0603Metric
C16: 2.2uF; C_0603_1608Metric
C17, C18: 22uF; C_0402_1005Metric
C32: 2.2uF; C_0201_0603Metric
C33, C34, C35, C36: 20pF; C_0201_0603Metric
Card1: TF-01A; TF-SMD_TF-01A; LCSC Part C91145
D1: LED; LED_0402_1005Metric
J1: Screw_Terminal_01x02; TerminalBlock_Xinya_XY308-2.54-2P_1x02_P2.54mm_Horizontal
J2, J3: Conn_01x03; PinHeader_1x03_P2.54mm_Vertical
L4: FCM1608KF-601T03; L0603; LCSC Part C141723
L5: DFE252012F-1R0M=P2; L2520; LCSC Part C435392
L6: XFL4020-152MEC; IND-SMD_L4.0-W4.0-A; LCSC Part C3033018
L7: YHNR3015-5R6M; IND-SMD_L3.0-W3.0; LCSC Part C18236327
R1, R2: 5.1K; R_0201_0603Metric
R3: 383; R_0201_0603Metric
R4: 5.23K; R_0201_0603Metric
R5: 30.1K; R_0201_0603Metric
R6, R7, R8, R9, R10, R11, R12, R13, R16, R17, R18, R19, R20, R21, R22: 10K; R_0201_0603Metric
R14: 100K; R_0402_1005Metric
R15: 22.1K; R_0402_1005Metric
SW1, SW2: TS-1088-AR02016; SW-SMD_L3.9-W3.0-P4.45; LCSC Part C720477
U1: BQ25883RGER; VFQFPN-24_L4.0-W4.0-P0.50-BL-EP2.8; LCSC Part C544362
U2: ICM-45686; LGA-14_L3.0-W2.5-P0.50-TL; LCSC Part C22459454
U3: STM32F722RETx; LQFP-64_10x10mm_P0.5mm
U4: BMP580; LGA-10_L2.0-W2.0-P0.50-TL_BMP580; LCSC Part C22391138
U5: TPS63070RNMR; VQFN-HR-15_L3.0-W2.5-P0.50-BL_TPS63070RNMR; LCSC Part C109322
U6: LMR51430; SOT-23-6
USB1: TYPE-C 16PIN 2MD(073); USB-C-SMD_TYPE-C-6PIN-2MD-073; LCSC Part C2765186
X1: X322525MOB4SI; CRYSTAL-SMD_4P-L3.2-W2.5-BL; LCSC Part C9006
X2: Q13FC1350000400; FC-135R_L3.2-W1.5; LCSC Part C32346

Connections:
+3.3V: C17.1, C18.1, C19.1, C20.1, C21.1, C22.1, C23.1, C24.1, C25.1, C26.1, C27.1, C28.1, C29.1, C30.1, C31.1, Card1.4 (VDD), L4.2, L7.2, R7.2, R8.2, R9.2, R10.2, R11.2, R16.2, R17.2, R18.2, R19.2, R20.2, R21.2, SW2.1, U2.5 (VDDIO), U2.8 (VDD), U3.1 (VBAT), U3.19 (VDD), U3.32 (VDD), U3.48 (VDD), U3.64 (VDD), U4.1 (VDDIO), U4.10 (VDD)
+5V: C10.1, C11.1, C12.1, C13.1, J2.1, J3.1, R13.1, U5.5 (FB), U5.7 (Vout), U5.8 (Vout)
/BMP_INT: U3.62 (PB9), U4.7 (INT)
/BOOT: R22.2, SW2.2, U3.60 (BOOT0)
/BQ_CE: U1.3 (~CE), U3.61 (PB8)
/BQ_INT: R11.1, U1.6 (~INT), U3.57 (PB5)
/BQ_PG: R8.1, U1.9 (~PG)
/BTST: C4.1, L5.1, U1.17 (SW), U1.18 (SW)
/HSE_IN: C33.1, U3.5 (PH0), X1.1 (OSC1)
/HSE_OUT: C34.1, U3.6 (PH1), X1.3 (OSC2)
/I2C_SCL: R10.1, U1.5 (SCL), U3.58 (PB6), U4.2 (SCK)
/I2C_SDA: R9.1, U1.4 (SDA), U3.59 (PB7), U4.4 (SDI)
/ICM_CS: U2.12 (AP_CS), U3.20 (PA4)
/ICM_INT1: U2.4 (INT1/INT), U3.24 (PC4)
/ICM_INT2: U2.9 (INT2/FSYNC/CLKIN), U3.25 (PB0)
/ICM_SCK: U2.13 (AP_SCL/AP_SCLK), U3.21 (PA5)
/ICM_SDI: U2.14 (AP_SDA/AP_SDIO/AP_SDI), U3.23 (PA7)
/ICM_SDO: U2.1 (AP_SDO/AP_AD0), U3.22 (PA6)
/LSE_IN: C35.1, U3.3 (PC14), X2.1
/LSE_OUT: C36.1, U3.4 (PC15), X2.2
/RESET: C37.2, SW1.2, U3.7 (NRST)
/SD_CD: Card1.9 (CD), U3.55 (PB3)
/SD_CLK: Card1.5 (CLK(SCLK)), R21.1, U3.53 (PC12)
/SD_CMD: Card1.3 (CMD(DI)), R20.1, U3.54 (PD2)
/SD_DAT0: Card1.7 (DAT0(D0)), R16.1, U3.39 (PC8)
/SD_DAT1: Card1.8 (DAT1(RSV)), R17.1, U3.40 (PC9)
/SD_DAT2: Card1.1 (DAT2(RSV)), R18.1, U3.51 (PC10)
/SD_DAT3: Card1.2 (CDDAT3(CS)), R19.1, U3.52 (PC11)
/SERVO1: J2.2, U3.14 (PA0)
/SERVO2: J3.2, U3.15 (PA1)
/USB_DN: U3.44 (PA11), USB1.5 (DN2), USB1.7 (DN1)
/USB_DP: U3.45 (PA12), USB1.6 (DP1), USB1.8 (DP2)
BAT+: C2.1, J1.1, U1.13 (BAT), U1.14 (BAT)
GND: C1.2, C2.2, C3.2, C5.2, C6.2, C7.2, C8.2, C9.2, C10.2, C11.2, C12.2, C13.2, C14.2, C16.2, C17.2, C18.2, C19.2, C20.2, C21.2, C22.2, C23.2, C24.2, C25.2, C26.2, C27.2, C28.2, C29.2, C30.2, C31.2, C32.2, C33.2, C34.2, C35.2, C36.2, C37.1, Card1.6 (VSS), Card1.10 (GND), Card1.11 (GND), Card1.12 (GND), Card1.13 (GND), J1.2, J2.3, J3.3, R1.2, R2.2, R3.2, R5.1, R6.1, R15.1, R22.1, SW1.1, U1.19 (GND), U1.20 (GND), U1.25 (EP), U2.6 (GND), U3.12 (VSSA), U3.18 (VSS), U3.31 (VSS), U3.47 (VSS), U3.63 (VSS), U4.3 (VSS), U4.5 (SDO), U4.6 (CSB), U4.8 (VSS), U4.9 (VSS), U5.4 (GND), U5.6 (FB2), U5.10 (PGND), U5.15 (Vsel), U6.1 (GND), USB1.1 (GND), USB1.12 (GND), USB1.13 (SHELL), USB1.14 (SHELL), X1.2 (GND), X1.4 (GND)
unnamed: C5.1, L5.2, U1.21 (PMID), U1.22 (PMID)
unnamed: D1.2 (A), R7.1
unnamed: D1.1 (K), U1.2 (STAT)
unnamed: C4.2, U1.12 (BTST)
unnamed: R3.1, U1.8 (ILIM)
unnamed: R4.1, R5.2, R6.2, U1.7 (TS)
unnamed: C32.1, U3.30 (VCAP_1)
unnamed: L4.1, U3.13 (VDDA)
unnamed: R12.1, U5.1 (PS/SYNC), U5.14 (EN)
unnamed: L6.2, U5.11 (L1)
unnamed: L6.1, U5.9 (L2)
unnamed: R13.2, U5.2 (PG)
unnamed: C14.1, U5.3 (Vaux)
unnamed: C15.1, U6.6 (CB)
unnamed: R14.1, R15.2, U6.4 (FB)
unnamed: C15.2, L7.1, R14.2, U6.2 (SW)
unnamed: R1.1, USB1.4 (CC1)
unnamed: R2.1, USB1.10 (CC2)
VBUS: C1.1, U1.23 (VBUS), USB1.2 (VBUS), USB1.11 (VBUS)
VREGN: C3.1, R4.2, U1.11 (REGN)
VSYS: C6.1, C7.1, C8.1, C9.1, C16.1, R12.2, U1.15 (SYS), U1.16 (SYS), U5.12 (Vin), U5.13 (Vin), U6.3 (VIN), U6.5 (EN)

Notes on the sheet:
Simple Flight Controller
Pressure Sensor
Decoupling
3.3V Buck
Buttons
IMU
USB-C
Servos
Battery Charger
STM32
Crystals
microSD Card
5V Buck-Boost

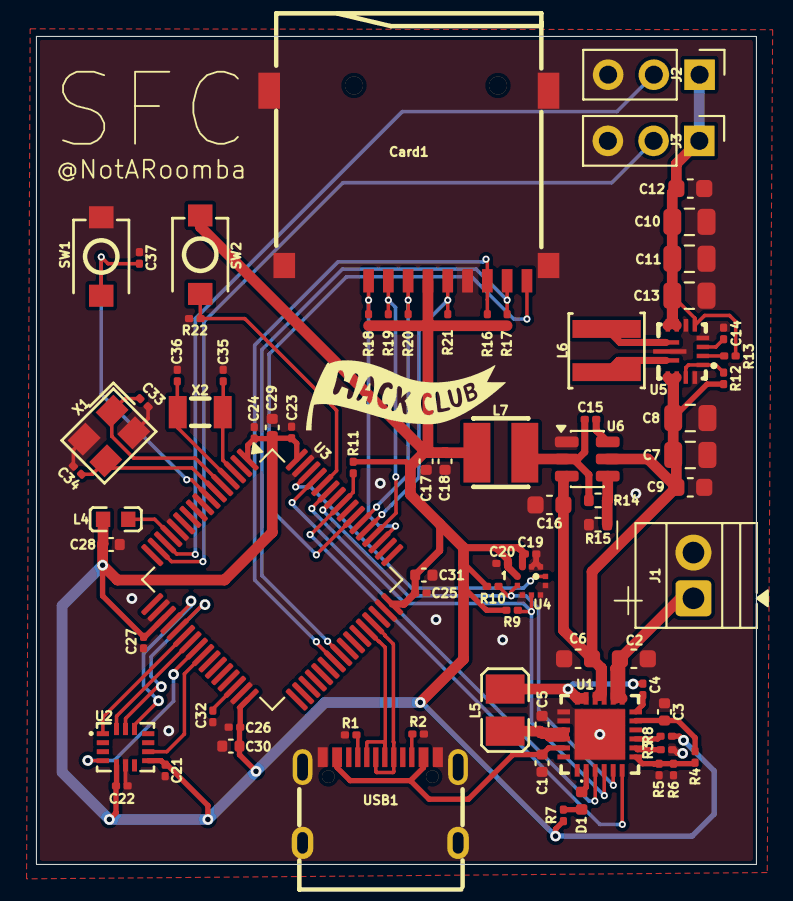
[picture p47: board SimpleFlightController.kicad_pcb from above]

Board: 2 copper layers, 40.0 x 46.0 mm, 79 parts (0 on the bottom side), 55 nets.

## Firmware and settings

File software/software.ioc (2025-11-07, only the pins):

Mcu.UserName=STM32F722RETx
PA0-WKUP.Signal=S_TIM2_CH1_ETR
PA1.Signal=S_TIM2_CH2
PA11.Signal=USB_OTG_FS_DM
PA12.Signal=USB_OTG_FS_DP
PA4.Signal=SPI1_NSS
PA5.Signal=SPI1_SCK
PA6.Signal=SPI1_MISO
PA7.Signal=SPI1_MOSI
PB0.GPIO_Label=ICM_INT2
PB0.Signal=GPXTI0
PB3.GPIO_Label=SD_CS
PB3.Signal=GPIO_Input
PB5.GPIO_Label=BQ_INT
PB5.Signal=GPXTI5
PB6.Signal=I2C1_SCL
PB7.Signal=I2C1_SDA
PB8.GPIO_Label=BQ_CE
PB8.Signal=GPIO_Output
PB9.GPIO_Label=BMP_INT
PB9.Signal=GPXTI9
PC10.Signal=SDMMC1_D2
PC11.Signal=SDMMC1_D3
PC12.Signal=SDMMC1_CK
PC14-OSC32_IN.Signal=RCC_OSC32_IN
PC15-OSC32_OUT.Signal=RCC_OSC32_OUT
PC4.GPIO_Label=ICM_INT1
PC4.Signal=GPXTI4
PC8.Signal=SDMMC1_D0
PC9.Signal=SDMMC1_D1
PD2.Signal=SDMMC1_CMD
PH0-OSC_IN.Signal=RCC_OSC_IN
PH1-OSC_OUT.Signal=RCC_OSC_OUT

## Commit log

2025-10-26 add kicad stard and omponents
    [SimpleFlightController.kicad_pcb, SimpleFlightController.kicad_sch]
2025-10-27 finished the 5v buck boost section
    [SimpleFlightController.kicad_sch]
2025-10-27 added more stuff
    [SimpleFlightController.kicad_sch]
2025-11-02 schematic done
    [SimpleFlightController.kicad_sch]
2025-11-06 finish guide and board
    [SimpleFlightController.kicad_pcb, SimpleFlightController.kicad_sch, bom.csv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]
2025-11-06 add readme and bom
    [bom.csv]
2025-11-06 bo mand cart
    [bom.csv]
2025-11-07 add stm32 programmign guide
2025-11-11 update image paths and 3d render
    [SimpleFlightController.kicad_pcb]
2025-11-11 start blender render and hc flag
    [SimpleFlightController.kicad_pcb]
2025-11-11 fix missing images
    [SimpleFlightController.kicad_pcb]
2025-11-22 flip led
    [SimpleFlightController.kicad_pcb, SimpleFlightController.kicad_sch]
